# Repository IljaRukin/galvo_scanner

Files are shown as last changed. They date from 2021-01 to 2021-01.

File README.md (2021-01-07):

# galvo scanner

setup for displaying a still images

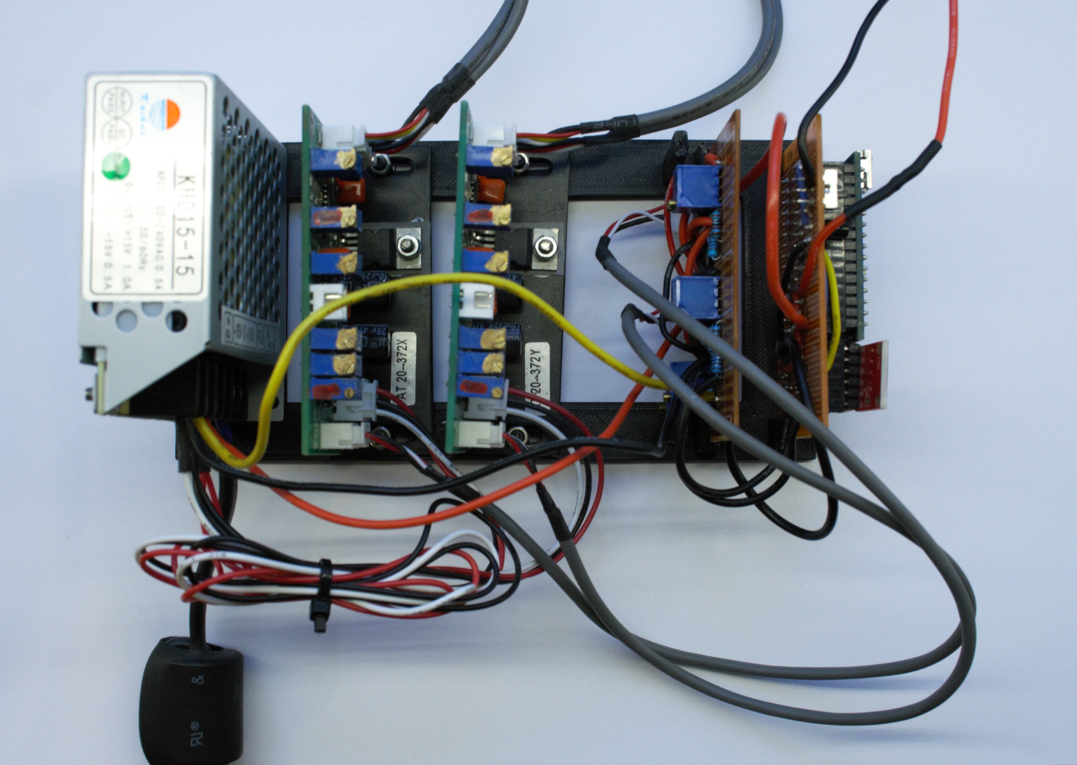
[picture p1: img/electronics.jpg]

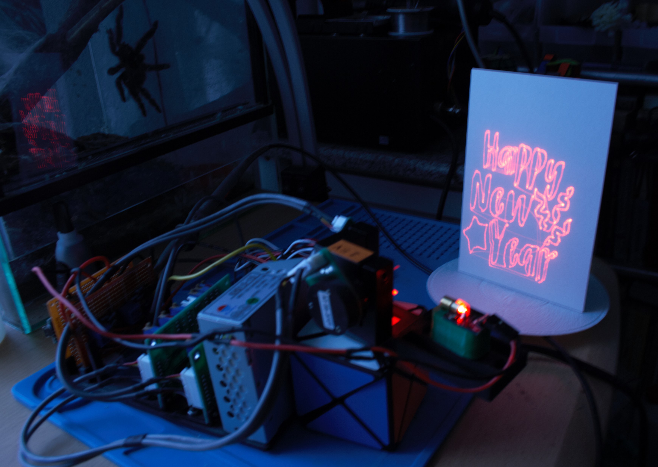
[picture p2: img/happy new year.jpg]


here is a video demonstration: \
[](https://youtu.be/ha9n86Zofew)

the scanner is composed of a power supply, two mirror galvanometers and their control units from china. the control units are controled with an differential Signal with +/-5V max. \
this signal is generated from an analog signal using one inverting op-amp to generate the negative output and one op-amp as a voltage buffer for the original signal for each axis. \
the actual analog signal is stored as a 12bit value on an arduino nano and communicated to two mcp4725 DACs over I2C. \
the image is drawn by rederecting a laser pointer by the galvo mirrors and turning the laser pointer on and off on Pin D13.

the following programs are supplied:
- a short sketch to run the galvo scanner with use of arduino libraries: "galvo"
- a faster version by directly controling the registers on the atmega328p: "galvo_lowlevel"
- the faster version with line tracing by a predefined step size instead of directly jumping between stored points: "galvo_lowlevel_trace"

the procedure to generate coordinate points form any svg is as follows:
- in inkscape set svg size to 1inch x 1inch and export it as graphics.hpgl with 4095dpi x 4095dpi, this generates the coordinates
- run script "convert.py" to convert the graphics.hpgl file to graphics.cpp, this reformats the coordinate points into three arrays for the x/y-coordinates and if the laser has to be on/off at that particular coordinate (the separate steps and their output are visualized in "hpgl to hex.ipynb") \
an example is stored in the folder: "svg to coordinates"

## issues
my galvo does respond quite slowly and not linear even after calibration. when using the first two scripts ("galvo" & "galvo_lowlevel") long straight lines get distorted and the image can only be displayed if an additional delay between each coordinate change is set. The third script circumvents this issues by tracing long lines with many small steps. there is a tradeoff between the step size and the frame rate, such that the path has either distinct sharp steps or is only observable in a long exposure with a camera.

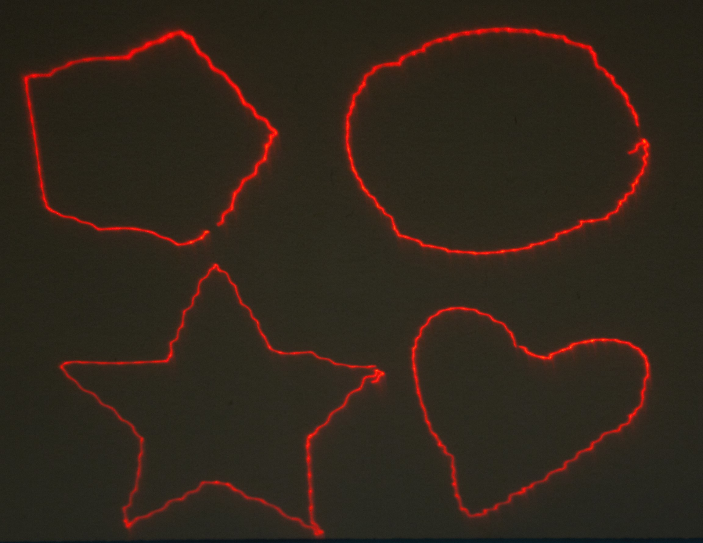
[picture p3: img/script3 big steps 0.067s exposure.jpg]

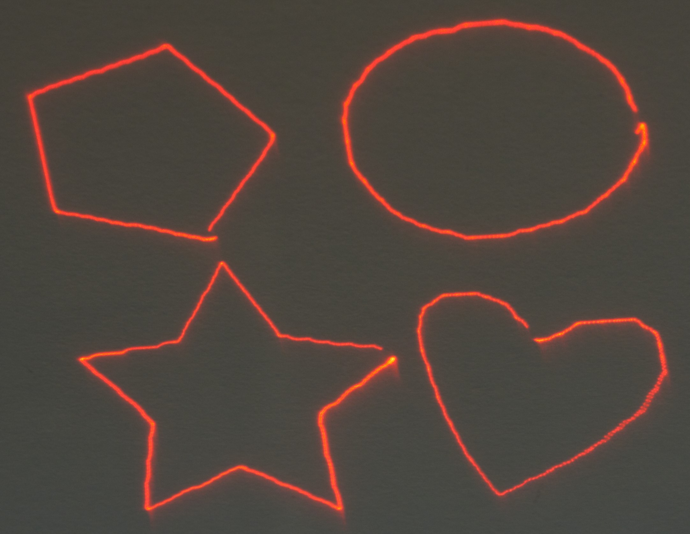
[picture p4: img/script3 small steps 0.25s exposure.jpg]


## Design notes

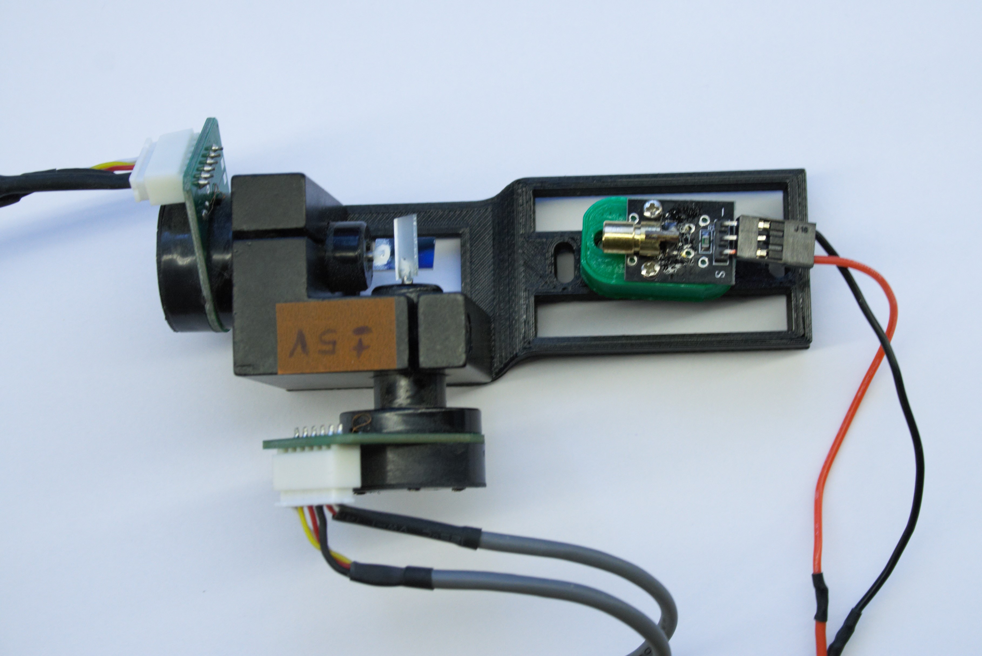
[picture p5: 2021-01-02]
img/galvo_mirrors_1.jpg

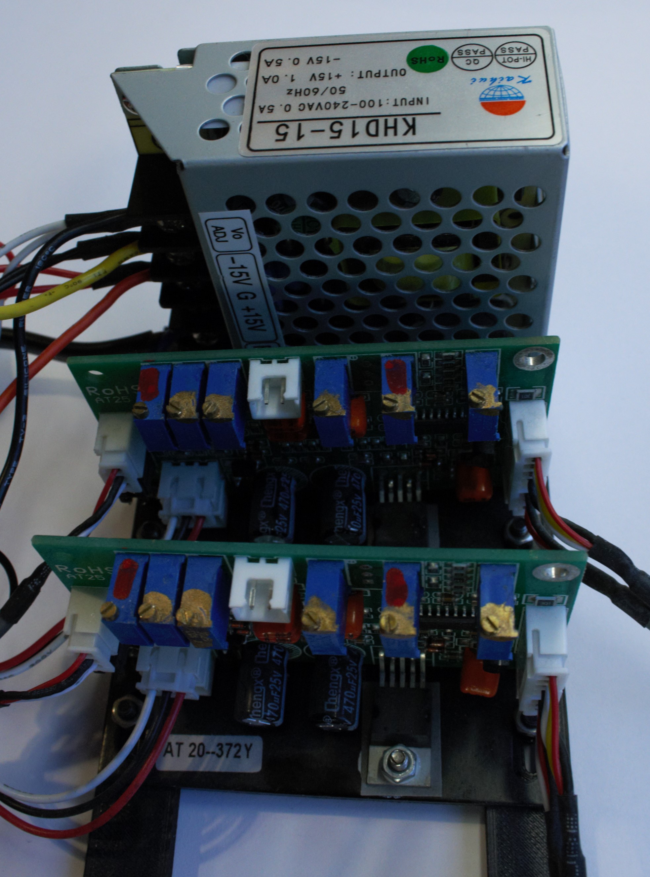
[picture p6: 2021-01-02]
img/power_and_control.jpg

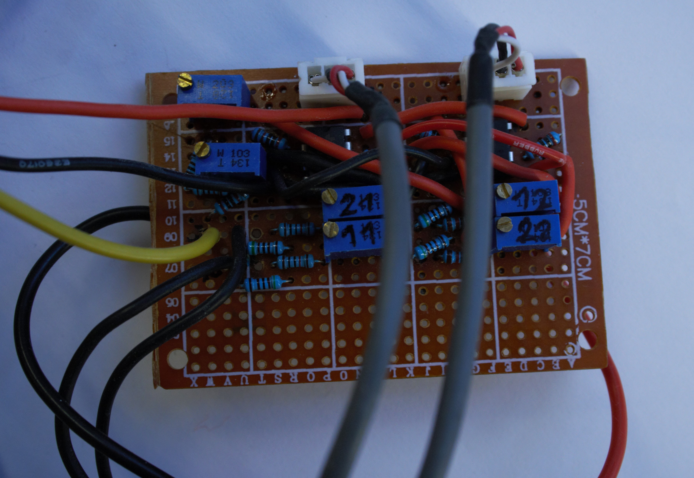
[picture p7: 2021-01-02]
img/differential_signal_generator.jpg

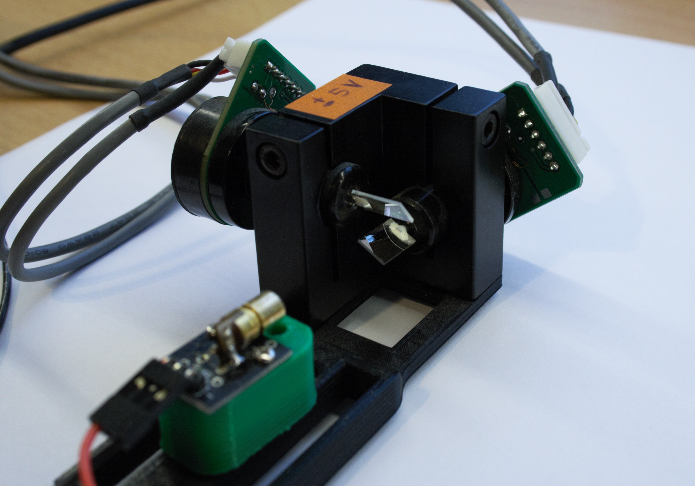
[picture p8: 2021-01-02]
img/galvo_mirrors_2.jpg

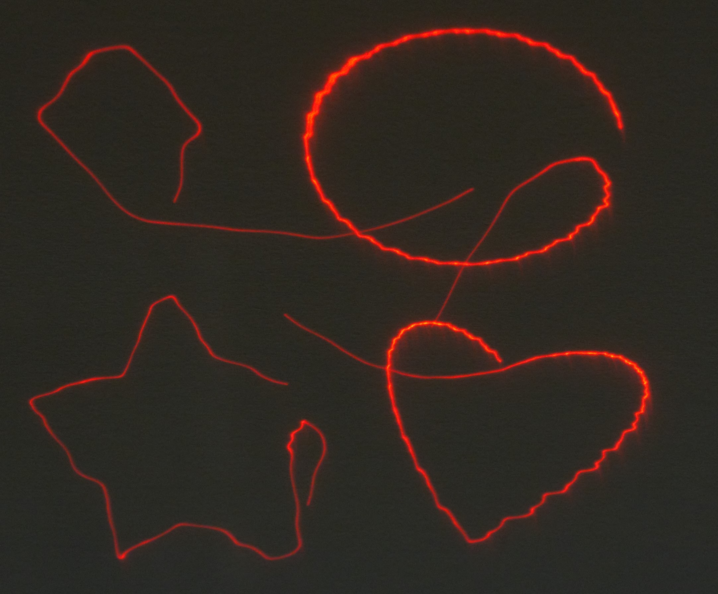
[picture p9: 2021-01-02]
img/script2.jpg

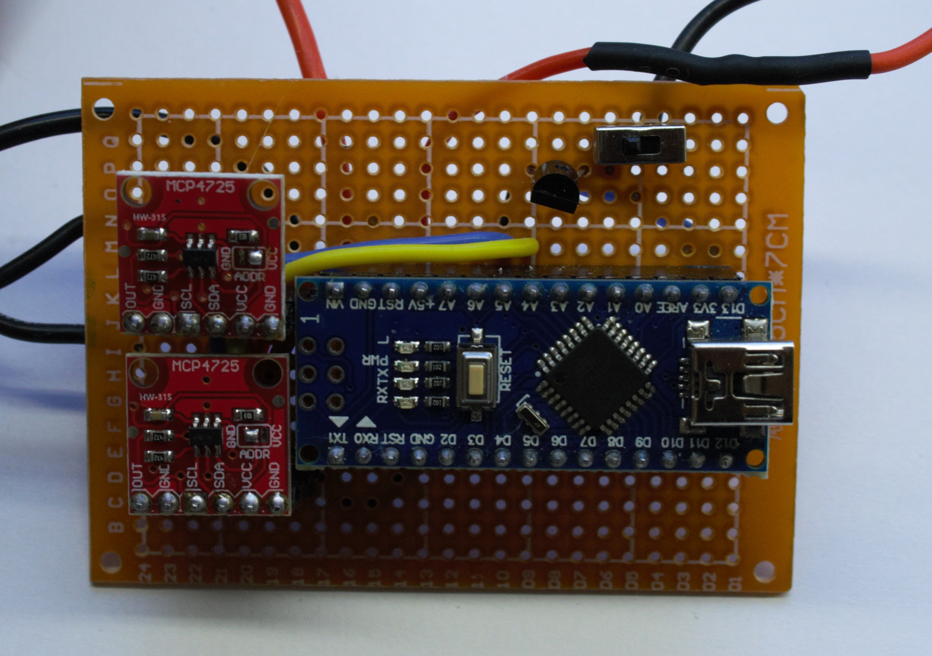
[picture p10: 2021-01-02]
img/analog_signal_generator.jpg

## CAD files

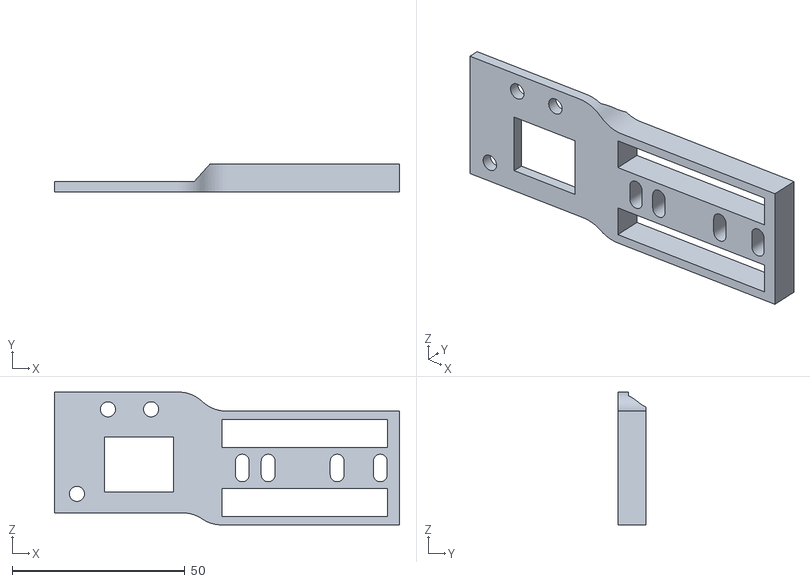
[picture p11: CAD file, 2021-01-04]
3d files/galvo and laser mount.stl
100.0 x 8.00 x 38.5

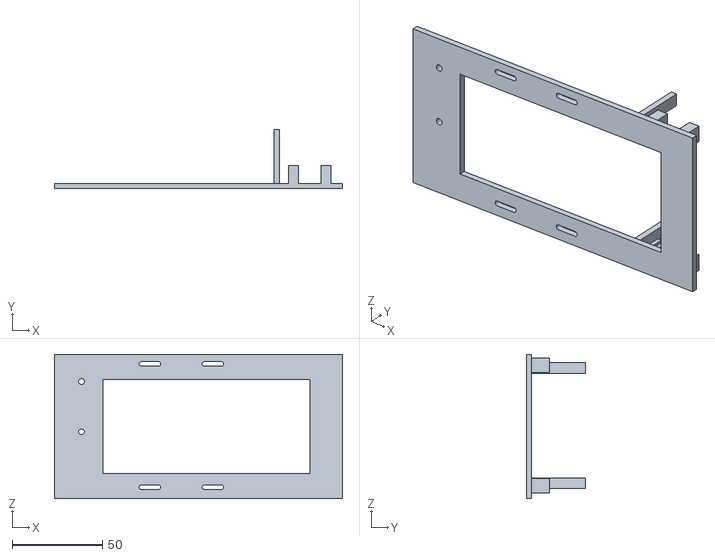
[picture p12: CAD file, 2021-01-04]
3d files/electronics mount.stl
160.0 x 33.0 x 80.0

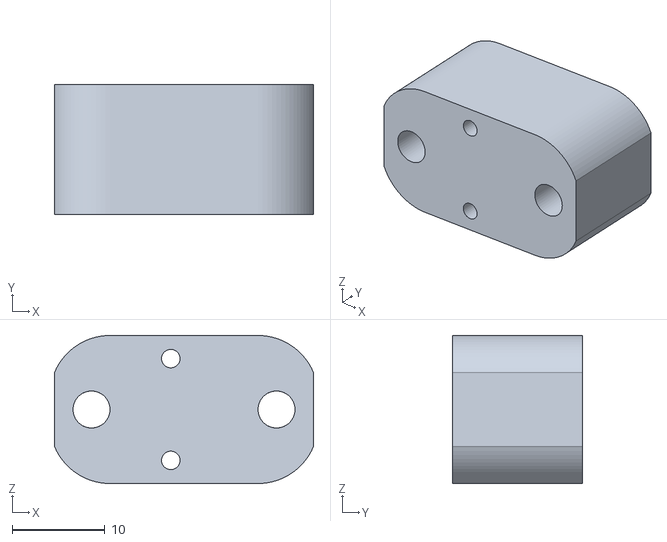
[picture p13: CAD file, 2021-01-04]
3d files/laser base mount.stl
28.0 x 14.0 x 16.0

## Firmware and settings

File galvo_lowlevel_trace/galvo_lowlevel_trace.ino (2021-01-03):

/*
 * control galvo mirrors using 2 MCP4725 DACs
 * 
 * MCP4725
 * 5.93Hz sine wave
 * 
 *  VCC   GND  Vout
 *    |    |    |
 * |---------------|
 * |     AJW0      |
 * |---------------|
 *    |    |    |
 *   SDA  CLK   A0
 * 
 * circuit board:
 * smoothing capacitor
 * pullup for SDA/SCL (pads on bottom [connected])
 * pullup/pulldown for A0 (pads on top [disconnected]) => sets Adress
 * A0=GND: Adress=0x60 /// A0=VCC: Adress=0x61
 * 
 */

#include <avr/io.h>
#include <util/delay.h>
#include "TWI.h"

#define F_CPU 16000000
#define LASER 13
#define STEP 128
#define STEP_INV 1/STEP

uint32_t idx = 0;
uint16_t x = 0;
uint16_t y = 0;
uint16_t next_x = 0;
uint16_t next_y = 0;


//graphic
#include "graphic.c"


/*
//cube
#define ARR_LENGTH 4
const bool pen[ARR_LENGTH] = {1,1,1,1};
const uint16_t xval[ARR_LENGTH] PROGMEM = {0, 4095, 4095, 0};
const uint16_t yval[ARR_LENGTH] PROGMEM = {0, 0, 4095, 4095};
*/

/*
//circle
#include <avr/pgmspace.h>
#define ARR_LENGTH 255
const bool pen[ARR_LENGTH] = {1,1,1,1,1,1,1,1,1,1,1,1,1,1,1,1,1,1,1,1,1,1,1,1,1,1,1,1,1,1,1,1,1,1,1,1,1,1,1,1,1,1,1,1,1,1,1,1,1,1,1,1,1,1,1,1,1,1,1,1,1,1,1,1,1,1,1,1,1,1,1,1,1,1,1,1,1,1,1,1,1,1,1,1,1,1,1,1,1,1,1,1,1,1,1,1,1,1,1,1,1,1,1,1,1,1,1,1,1,1,1,1,1,1,1,1,1,1,1,1,1,1,1,1,1,1,1,1,1,1,1,1,1,1,1,1,1,1,1,1,1,1,1,1,1,1,1,1,1,1,1,1,1,1,1,1,1,1,1,1,1,1,1,1,1,1,1,1,1,1,1,1,1,1,1,1,1,1,1,1,1,1,1,1,1,1,1,1,1,1,1,1,1,1,1,1,1,1,1,1,1,1,1,1,1,1,1,1,1,1,1,1,1,1,1,1,1,1,1,1,1,1,1,1,1,1,1,1,1,1,1,1,1,1,1,1,1,1,1,1,1,1,1,1,1,1,1,1,1,1,1,1,1,1,1,};
const uint16_t xval[ARR_LENGTH] PROGMEM = {2048,2098,2148,2199,2249,2299,2349,2399,2448,2498,2547,2596,2644,2692,2740,2787,2834,2880,2926,2971,3016,3060,3104,3147,3189,3230,3271,3311,3351,3389,3427,3464,3500,3535,3569,3602,3635,3666,3697,3726,3754,3782,3808,3833,3857,3880,3902,3923,3943,3961,3979,3995,4010,4024,4036,4048,4058,4067,4074,4081,4086,4090,4093,4095,4095,4094,4092,4088,4084,4078,4071,4062,4053,4042,4030,4017,4002,3987,3970,3952,3933,3913,3891,3869,3845,3821,3795,3768,3740,3711,3681,3651,3619,3586,3552,3517,3482,3445,3408,3370,3331,3291,3251,3210,3168,3125,3082,3038,2994,2949,2903,2857,2811,2764,2716,2668,2620,2571,2522,2473,2424,2374,2324,2274,2224,2174,2123,2073,2022,1972,1921,1871,1821,1771,1721,1671,1622,1573,1524,1475,1427,1379,1331,1284,1238,1192,1146,1101,1057,1013,970,927,885,844,804,764,725,687,650,613,578,543,509,476,444,414,384,355,327,300,274,250,226,204,182,162,143,125,108,93,78,65,53,42,33,24,17,11,7,3,1,0,0,2,5,9,14,21,28,37,47,59,71,85,100,116,134,152,172,193,215,238,262,287,313,341,369,398,429,460,493,526,560,595,631,668,706,744,784,824,865,906,948,991,1035,1079,1124,1169,1215,1261,1308,1355,1403,1451,1499,1548,1597,1647,1696,1746,1796,1846,1896,1947,1997,};
const uint16_t yval[ARR_LENGTH] PROGMEM = {4095,4094,4093,4089,4085,4079,4073,4065,4055,4045,4033,4020,4006,3991,3974,3957,3938,3918,3897,3875,3851,3827,3801,3775,3747,3719,3689,3658,3627,3594,3561,3526,3491,3455,3418,3380,3341,3301,3261,3220,3178,3136,3093,3049,3005,2960,2915,2869,2822,2775,2728,2680,2632,2584,2535,2486,2436,2386,2337,2287,2236,2186,2136,2085,2035,1984,1934,1884,1833,1783,1733,1684,1634,1585,1536,1487,1439,1391,1343,1296,1249,1203,1158,1112,1068,1024,980,938,896,854,814,774,735,696,659,622,586,551,518,484,452,421,391,362,334,307,281,256,232,209,187,167,148,129,112,96,82,68,56,45,35,26,19,13,8,4,1,0,0,1,4,8,13,19,26,35,45,56,68,82,96,112,129,148,167,187,209,232,256,281,307,334,362,391,421,452,484,518,551,586,622,659,696,735,774,814,854,896,938,980,1024,1068,1112,1158,1203,1249,1296,1343,1391,1439,1487,1536,1585,1634,1684,1733,1783,1833,1884,1934,1984,2035,2085,2136,2186,2236,2287,2337,2386,2436,2486,2535,2584,2632,2680,2728,2775,2822,2869,2915,2960,3005,3049,3093,3136,3178,3220,3261,3301,3341,3380,3418,3455,3491,3526,3561,3594,3627,3658,3689,3719,3747,3775,3801,3827,3851,3875,3897,3918,3938,3957,3974,3991,4006,4020,4033,4045,4055,4065,4073,4079,4085,4089,4093,4094,};
*/

void init(void)
{
  TWIInit();
  
  DDRB |= (1<<PB5);
  //PORTB &= ~(1<<PB5);
  PORTB |= (1<<PB5);
  _delay_ms(500);
}

//void point(uint16_t x, uint16_t y){
void point(void){
      TWIStart();
      //TWIWrite(0x60);
      TWIWrite(0xC0);
      TWIWrite( x >> 8 );
      TWIWrite( x & B11111111 );
      TWIStop();
  
      TWIStart();
      //TWIWrite(0x61);
      TWIWrite(0xC2);
      TWIWrite( y >> 8 );
      TWIWrite( y & B11111111 );
      TWIStop();
}

//void trace_line_2d(uint16_t x, uint16_t y, uint16_t next_x, uint16_t next_y) {
void trace_line_2d() {
  //interpolate line (bresensham line algorithm)
  //step along the long side and correct the shorter side
  uint16_t iii;
  float over;
  int16_t ddx = next_x - x;
  int16_t ddy = next_y - y;
  int16_t dirx = ddx > 0 ? STEP : -STEP;
  int16_t diry = ddy > 0 ? STEP : -STEP;
  uint16_t dx = abs(floor(ddx*STEP_INV));
  uint16_t dy = abs(floor(ddy*STEP_INV));
  
  //if ((dx!=0) || (dy!=0)){
    if (dx > dy) {
      over = dx / 2;
      for (uint16_t i = 0; i < dx; i++) {
        x += dirx;
        over += dy;
        if (over >= dx) {
          over -= dx;
          y += diry;
        }
        //point(x,y);
        point();
      }
    }
    else {
      over = dy / 2;
      for (iii = 0; iii < dy; iii++) {
        y += diry;
        over += dx;
        if (over >= dy) {
          over -= dy;
          x += dirx;
        }
        //point(x,y);
        point();
      }
    //}
  }
  x = next_x;
  y = next_y;
  point();
  return;
}

int main(void)
{
  init();
  while(true){
    for(idx=0;idx<ARR_LENGTH;idx++){
      PORTB = (pen[idx]<<PB5);
      
      next_x = pgm_read_word(xval+idx);
      next_y = pgm_read_word(yval+idx);
      //trace_line_2d(x,y,next_x,next_y);
      trace_line_2d();

      //_delay_ms(0.02);
    }
  }
}
